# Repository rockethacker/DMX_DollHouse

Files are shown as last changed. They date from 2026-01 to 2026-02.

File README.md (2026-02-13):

# DMX_DollHouse
DMX Controller for Haunted Doll House

# Development Environment Setup
1. Install Github Desktop from https://desktop.github.com/download/
2. Open Github Desktop and sign in. Create account if needed.
3. In Github Desktop clone this repo
   1. "File --> Clone repository..."
   2. Select "URL" tab
   3. Enter "rockethacker/DMX_DollHouse" into URL field
   4. Note that this will clone to your documents folder
5. Install Arduino IDE from https://www.arduino.cc/en/software/#ide
6. Open Arduino IDE
7. Install board definition
   1. Open "Tools --> Board --> Boards Manager..."
   2. search for "esp"
   3. Install "esp32 by Espressif Systems" version 3.1.0
   4. If it times out, try this https://forum.arduino.cc/t/downloading-esp32-3-3-5-fails/1420739/7
8. Note that the above installations should take care of the CH340 driver installation. If not, follow https://learn.sparkfun.com/tutorials/how-to-install-ch340-drivers
9. Install Libraries
   1. Open "Tools --> Manage Libraries..."
   1. Install "esp_dmx by Mitch Weisbrod" version 4.1.0
      1. dmx read example won't compile, https://github.com/someweisguy/esp_dmx/issues/181#issuecomment-2619261884
      1. update uart.c to fork version
   1. Install "Freenove WS2812 Lib for ESP32" version 2.0.1
   2. Install "SparkFun Qwiic Relay Arduino Library" version 1.3.1
   3. Install "Adafruit SH110X" v2.1.14 with dependencies
10. Plug in Sparkfun Thing Plus via USB C cable
11. Select board by selecting "Tools --> Board --> esp32 --> SparkFun ESP32 Thing Plus C" 
12. Select port by selecting "Tools -->  Port --> COMxx" Where "xx" is the port your board is connected to (e.g. COM3)
13. Open this project by selecting "File --> Open..." and navigating to "Documents\GitHub\DMX_DollHouse\DMX_DollHouse.ino"

# Hardware
Parts are mostly from SparkFun. If you're in the DFW area and buy from Mouser you can get very fast, cheap delivery (sometimes overnight) via USPS
* https://www.sparkfun.com/sparkfun-esp32-thing-plus-dmx-to-led-shield.html
* https://www.sparkfun.com/sparkfun-thing-plus-esp32-wroom-usb-c.html
* https://www.sparkfun.com/feather-stackable-header-set.html
  * headers for thing plus
* https://www.adafruit.com/product/6313 - FeatherWing 128x64 OLED with pins
* https://www.sparkfun.com/sparkfun-qwiic-quad-relay.html
  * Discontinued product but available on Mouser
* This code supports WS2812 LEDs
* Power connection is a 5.5mm barrel jack with positive center pin.

# Pin & Channel Designations
* Pinouts for SparkFun Thing (SFT) Plus C. J1 is the 16 pin header. J7 is the 12 pin header.
* For some reason, the DMX board documentation had the D1/D1 pins swapped

| SFT Pin | SFT GPIO | SFT Name | Connected To  |
| --- | --- | --- | --- |
| J1-13 | 19 | POCI | DMX D0 |
| J1-12 | 23 | PICO | DMX D1 |
| J7-6 | 27 | 11 | DMX D2 |
| J1-2 | 17 | TX | DMX Transmit  |
| J1-3 | 16 | RX | DMX Receive |
| J1-1 | 4 | FREE | DMX Enable |
| J7-5 | 15 | 08 | OLED Button A |
| J7-3 | 14 | 04 | OLED Button B |
| J7-4 | 32 | 06 | OLED Button C |

# DMX Universe Channels
* All Channels are Offset by the the starting address (default is 0 offset)
* Lighting values are 0-255
* Relay commands are boolean >127 is TRUE

| Chan | Function |
| ---- | --- |
| 1 | LED0 Red |
| 2 | LED0 Green  |
| 3 | LED0 Blue |
| 4 | LED0 Dimmer |
| 5 | LED1 Red |
| 6 | LED1 Green  |
| 7 | LED1 Blue |
| 8 | LED1 Dimmer |
| 9 | LED2 Red |
| 10 | LED2 Green  |
| 11 | LED2 Blue |
| 12 | LED2 Dimmer |
| 13 | Relay 1 |
| 14 | Relay 2 |
| 15 | Relay 3 |
| 16 | Relay 4 |

# Troubleshooting Notes
* "SparkFun DMX Shield Library" makes some bad assumptions on how to detect the beginning of the DMX frames so isn't reliabloe for DMX reading

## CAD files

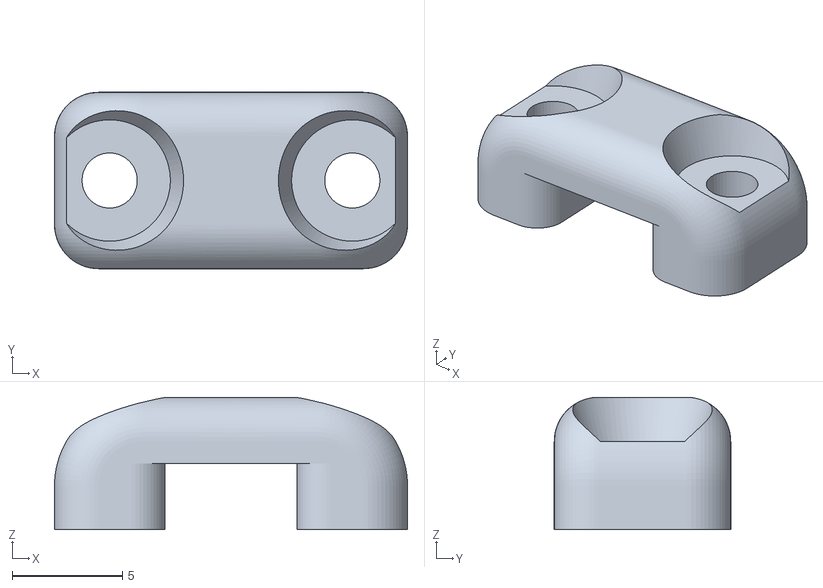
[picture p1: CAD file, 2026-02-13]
Enclosure/Clamp_LED.stl
16.0 x 8.00 x 6.00

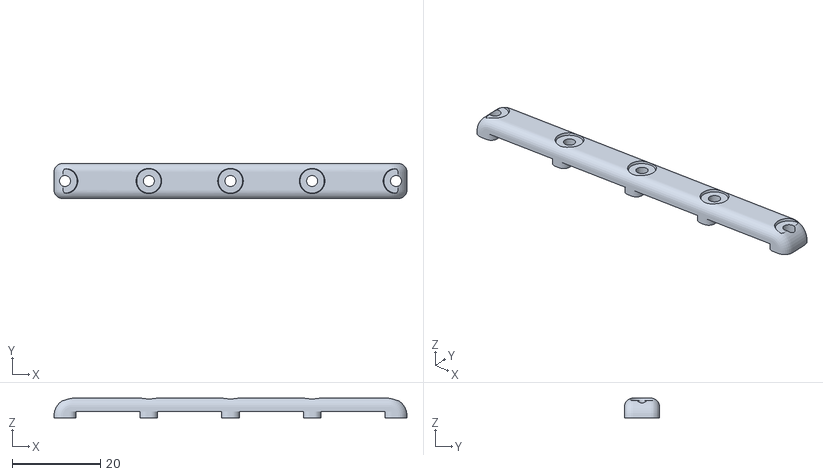
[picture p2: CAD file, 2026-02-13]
Enclosure/Clamp_Relay.stl
80.0 x 8.00 x 4.50

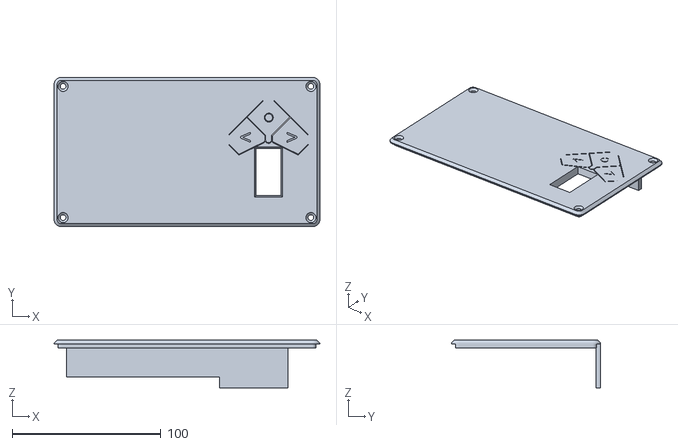
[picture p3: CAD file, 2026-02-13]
Enclosure/Box_Lid.stl
178.9 x 100.4 x 32.2

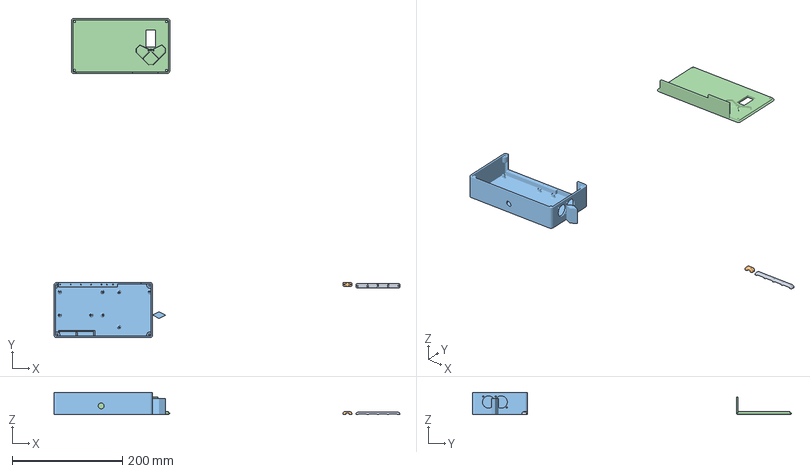
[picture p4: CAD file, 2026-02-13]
Enclosure/DollHouse.3mf
627.5 x 579.4 x 40.2 mm
Clamp_Relay.stl
Clamp_LED.stl
Box_Bottom.stl
Box_Lid.stl

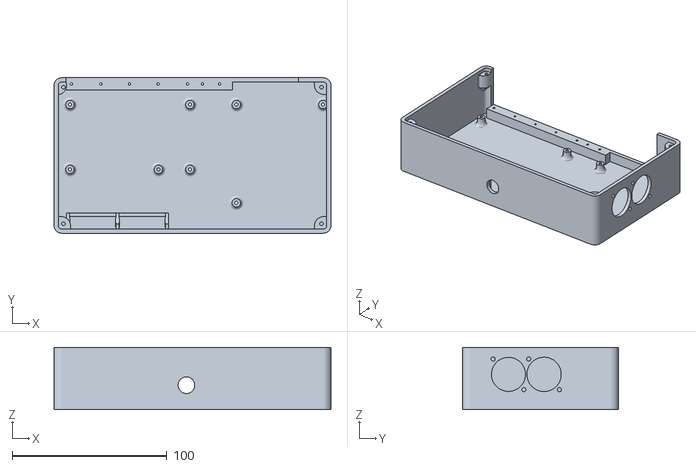
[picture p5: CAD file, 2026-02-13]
Enclosure/Box_Bottom.stl
178.9 x 100.4 x 40.2

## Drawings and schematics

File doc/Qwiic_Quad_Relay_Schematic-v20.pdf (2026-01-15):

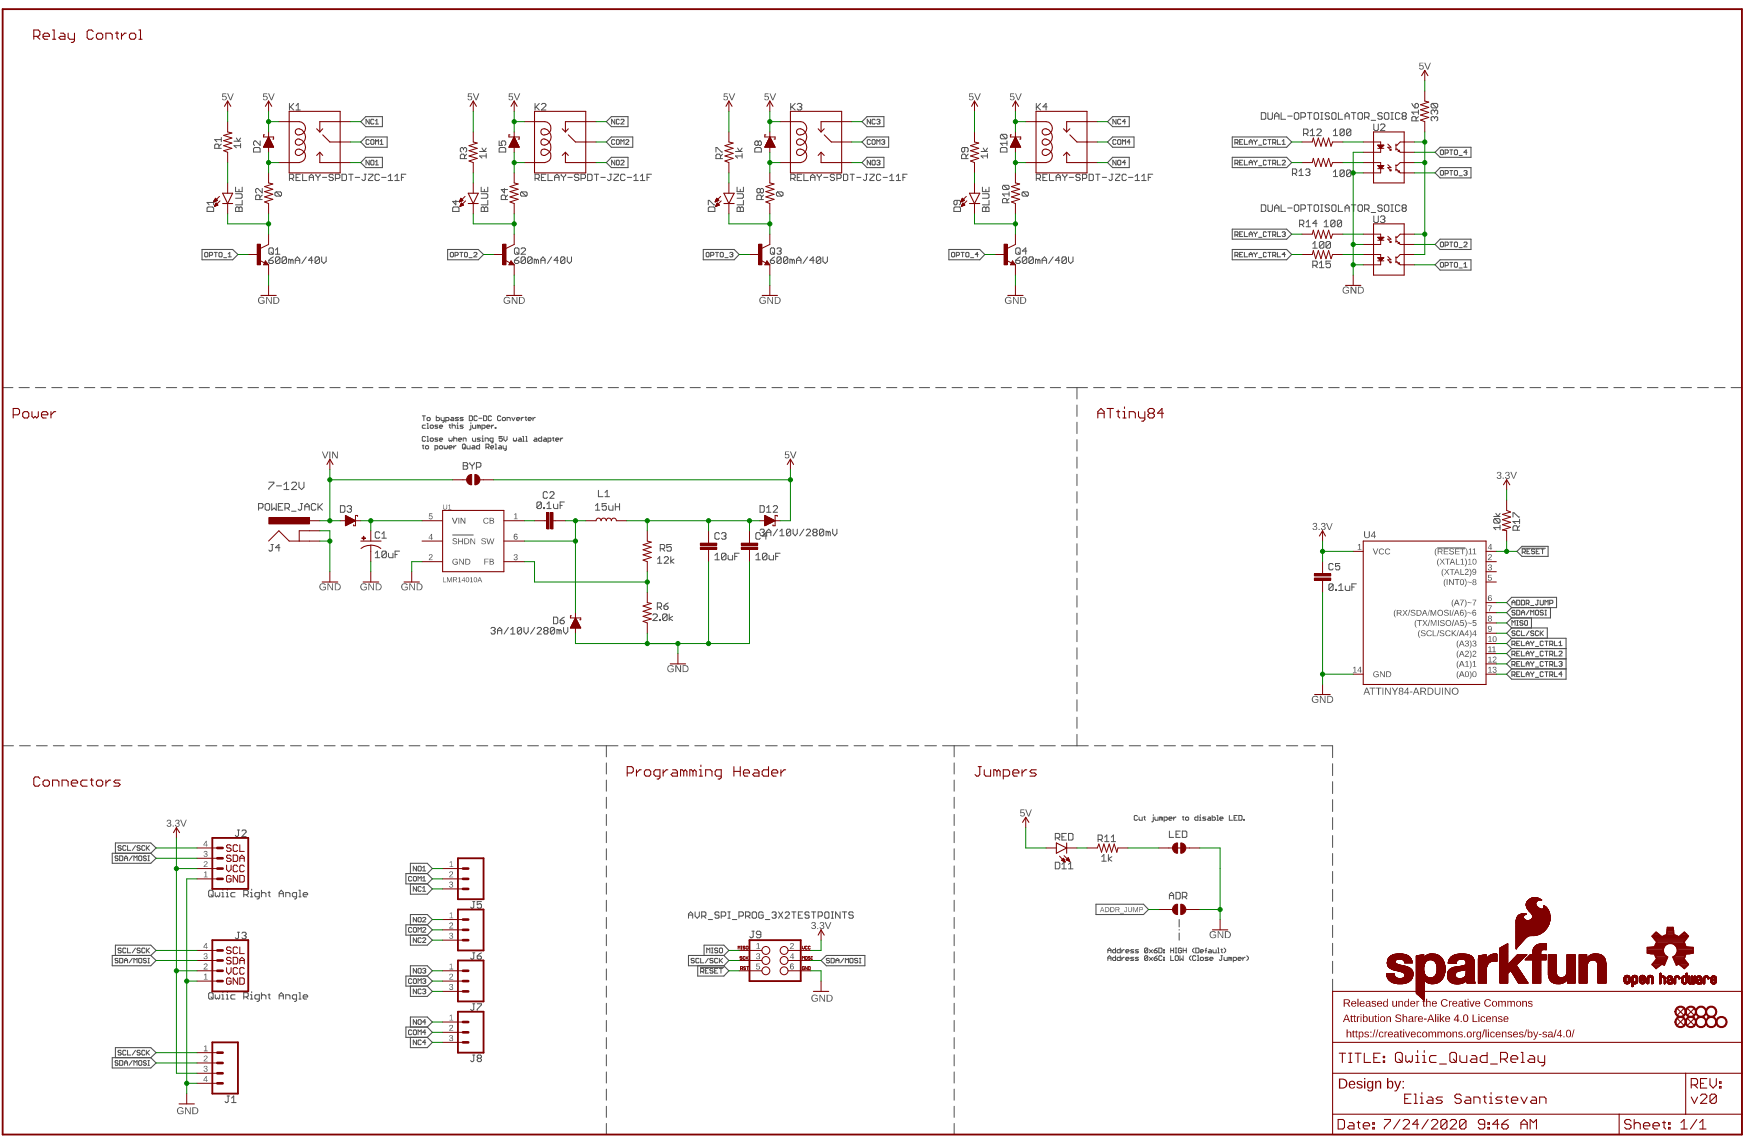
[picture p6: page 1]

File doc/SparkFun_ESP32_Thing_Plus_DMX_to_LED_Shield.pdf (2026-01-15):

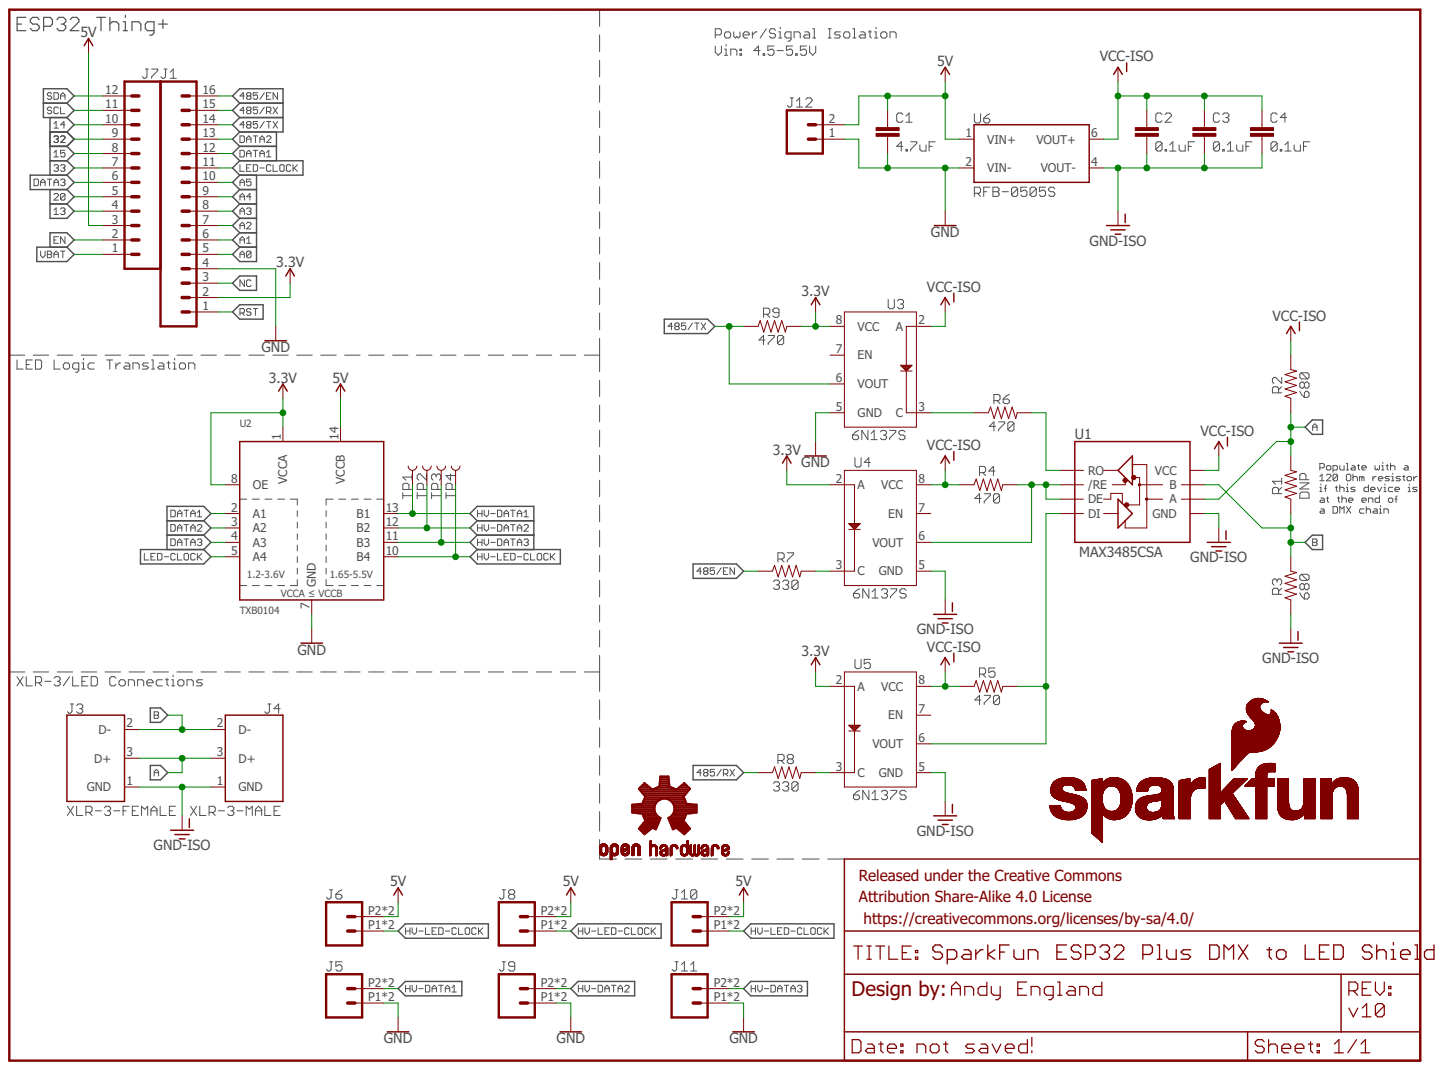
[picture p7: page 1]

Released under the Creative Commons Attribution Share-Alike 4.0 License https://creativecommons.org/licenses/by-sa/4.0/

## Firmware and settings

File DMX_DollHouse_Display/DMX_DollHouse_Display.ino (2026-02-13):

/*

  DMX Read

  This sketch allows you to read DMX from a DMX controller using a standard DMX
  shield, such SparkFun ESP32 Thing Plus DMX to LED Shield. This sketch was
  made for the Arduino framework!

  Created 9 September 2021
  By Mitch Weisbrod

  https://github.com/someweisguy/esp_dmx

*/
// DMX board libs
#include <Arduino.h>
#include <esp_dmx.h>
#include "Freenove_WS2812_Lib_for_ESP32.h"

//Relay Board Libs
#include <Wire.h>
#include "SparkFun_Qwiic_Relay.h"

//Display Libs
#include <SPI.h>
#include <Wire.h>
#include <Adafruit_GFX.h>
#include <Adafruit_SH110X.h>

// ==== DMX Init ==== //
// Define DMX bus
// Pins will differ between ESP32 models
int transmitPin = 17;
int receivePin = 16;
int enablePin = 4;

// Define port connected to DMX. ESP32 has either 2 or 3 ports.
// Port 0 is typically used to transmit serial data back to your Serial Monitor
dmx_port_t dmxPort = 1;

/* Now we want somewhere to store our DMX data. Since a single packet of DMX
  data can be up to 513 bytes long, we want our array to be at least that long.
  This library knows that the max DMX packet size is 513, so we can fill in the
  array size with `DMX_PACKET_SIZE`. */
byte data[DMX_PACKET_SIZE];

bool dmxIsConnected = false; //Connection status
unsigned long lastUpdate = millis(); //timer

// ==== LED Init ==== //
#define LEDS_COUNT  100 //Same LED count for all strips
// For some reason the documentation has pins 19 and 23 mixed up
#define LED0_PIN	19 //DMX board terminal D0. J1-pin 13 on Sparkfun Thing 
#define LED1_PIN	23 //DMX board terminal D1. J1-pin 12 on Sparkfun Thing
#define LED2_PIN	27 //DMX board terminal D2. J7-pin 6 on Sparkfun Thing

Freenove_ESP32_WS2812 LED0 = Freenove_ESP32_WS2812(LEDS_COUNT, LED0_PIN, 0, TYPE_GRB);
Freenove_ESP32_WS2812 LED1 = Freenove_ESP32_WS2812(LEDS_COUNT, LED1_PIN, 1, TYPE_GRB);
Freenove_ESP32_WS2812 LED2 = Freenove_ESP32_WS2812(LEDS_COUNT, LED2_PIN, 2, TYPE_GRB);

// ==== Relay Init ==== //
#define RELAY_ADDR 0x6D // Alternate address 0x6C

Qwiic_Relay quadRelay(RELAY_ADDR); 

// ==== Display Init ==== //
Adafruit_SH1107 display = Adafruit_SH1107(64, 128, &Wire);
uint16_t page_chan=0;
uint16_t page=0;
uint8_t data_val=0;

// ==== Program Init ==== //
//State machine states
enum states {
  DMX_SETUP, DMX_RUN, DMX
};

//Starting address in this DMX universe
//This device takes 16 channels
//baby board test is dmx start 1, ion perform is dmx 496
uint16_t dmxStartAddr = 496; 
int rate = 20; //rate in Hz

// a place to store packet information (not data)
dmx_packet_t packet;

void setup() {
  Serial.begin(115200); //Start serial monitor
  Serial.println("Initializing...");

// ==== DMX Init ==== //
  /* Install the DMX driver. Tell it which DMX port to use,
    what device configuration to use, and what DMX personalities it should have.
    If you aren't sure which configuration to use, you can use the macros
    `DMX_CONFIG_DEFAULT` to set the configuration to its default settings.
    This device is being setup as a DMX responder so it is likely that it should
    respond to DMX commands. It will need at least one DMX personality. Since
    this is an example, we will use a default personality which only uses 1 DMX
    slot in its footprint. */
  dmx_config_t config = DMX_CONFIG_DEFAULT;
  dmx_personality_t personalities[] = {
    {1, "Default Personality"}
  };
  int personality_count = 1;
  Serial.println("Installing dmx driver...");
  dmx_driver_install(dmxPort, &config, personalities, personality_count);
  Serial.println("dmx driver installed...");
  dmx_set_pin(dmxPort, transmitPin, receivePin, enablePin);

// ==== LED Init ==== //
  LED0.begin();
  LED0.setBrightness(0);
  LED1.begin();
  LED1.setBrightness(0);
  LED2.begin();
  LED2.setBrightness(0);

// ==== Relay Init ==== //
  Wire.begin(); 
  // Make sure the hardware is set up correctly.
  if(!quadRelay.begin())
    Serial.println("Check connections to Qwiic Relay.");
  else
    Serial.println("Ready to flip some switches.");
  
  // Make sure all relays are off
  quadRelay.turnAllRelaysOff(); 

// ==== Display Init ==== //
  delay(250); // wait for the OLED to power up
  display.begin(0x3C, true); // Address 0x3C default
  Serial.println("OLED begun");
  display.clearDisplay();
  display.setRotation(1);
  display.setTextSize(1);
  display.setTextColor(SH110X_WHITE);
}

void loop() {

  /* And now we wait! The DMX standard defines the amount of time until DMX
    officially times out. That amount of time is converted into ESP32 clock
    ticks using the constant `DMX_TIMEOUT_TICK`. If it takes longer than that
    amount of time to receive data, this if statement will evaluate to false. */
  if (dmx_receive(dmxPort, &packet, DMX_TIMEOUT_TICK)) {
    
    //we've received DMX data!
    unsigned long now = millis(); //Record when we received new data

    // If no DMX errors, do things
    if (!packet.err) {

      //On first packet, log successful connection
      if (!dmxIsConnected) {
        Serial.println("DMX is connected!");
        Serial.println(packet.size-1, DEC); //list DMX packet size
        dmxIsConnected = true;
      }
      
      // Print results to serial at rate
      if (now - lastUpdate > 1000/rate) {
        
        dmx_read(dmxPort, data, packet.size); //copy data into buffer
        
        /* Print the received start code - it's usually 0. */
        //Serial.printf("Start code is 0x%02X and slot 1 is 0x%02X\n", data[0], data[1]);
        
        // Data has been received, print out channel values to serial
        Serial.print(dmxStartAddr, DEC);
        Serial.print(" : ");
        for (uint16_t i = 0; i < 16; i++) {
          data_val = data[dmxStartAddr+i];
          if (data_val > 0xF){
            Serial.print(data_val, HEX);
          } else {
            Serial.print(" "); //pad single digit with space
            Serial.print(data_val, HEX);
          }
          Serial.print(" "); //space between entries
        }
       /*
        // write all channel values to serial
        for (uint16_t i = 1; i <=512; i++) {
            Serial.print(data[i], HEX);
            Serial.print(" ");
        }
        */
        
        Serial.println(" ");
        
        //Output color commands to LED strips
        LED0.setAllLedsColorData(data[dmxStartAddr+0], data[dmxStartAddr+1], data[dmxStartAddr+2]);
        LED0.setBrightness(data[dmxStartAddr+3]);
        LED0.show();
        LED1.setAllLedsColorData(data[dmxStartAddr+4], data[dmxStartAddr+5], data[dmxStartAddr+6]);
        LED1.setBrightness(data[dmxStartAddr+7]);
        LED1.show();
        LED2.setAllLedsColorData(data[dmxStartAddr+8], data[dmxStartAddr+9], data[dmxStartAddr+10]);
        LED2.setBrightness(data[dmxStartAddr+11]);
        LED2.show();

        //Output commands to relays
        if(data[dmxStartAddr+12]>127)
          quadRelay.turnRelayOn(1); 
        else
          quadRelay.turnRelayOff(1);

        if(data[dmxStartAddr+13]>127)
          quadRelay.turnRelayOn(2); 
        else
          quadRelay.turnRelayOff(2);

        if(data[dmxStartAddr+14]>127)
          quadRelay.turnRelayOn(3); 
        else
          quadRelay.turnRelayOff(3);

        if(data[dmxStartAddr+15]>127)
          quadRelay.turnRelayOn(4); 
        else
          quadRelay.turnRelayOff(4);

        // ==== Output to Display ==== //
       
        // Data has been received, print out channel values to display
        display.clearDisplay();
        display.setCursor(0,0);
        display.print("START: ");
        display.println(dmxStartAddr, DEC);
        for (uint16_t i = 0; i < 16; i++) {
          data_val = data[dmxStartAddr+i];
          if (data_val > 0xF){
            display.print(data_val, HEX);
          } else {
            display.print(" "); //pad single digit with space
            display.print(data_val, HEX);
          }
          display.print(" "); //space between entries
          if (i%4>=3) {display.println(" ");}
        }
        display.display(); // actually display all of the above

       /*
        //For each page. 8 channels per line. 8 lines per page.
        //for (page=0; page<=7; page++){
          display.clearDisplay();
          display.setCursor(105,0);
          display.print(page%8*64, DEC);
          display.setCursor(0,0);
          for (page_chan=0; page_chan <= 63; page_chan++){
            data_val = data[page%8*64+1];
            //If single digit, pad with space
            if (data_val > 0xF){
              display.print(data_val, HEX);
            } else {
              display.print(" ");
              display.print(data_val, HEX);
            }
            
            if (page_chan%8>=7) {display.println(" ");}
          }
          display.display(); // actually display all of the above
          page++;
          */
        //}
        lastUpdate = now;
      }
    } else {
      /* Oops! A DMX error occurred! Don't worry, this can happen when you first
        connect or disconnect your DMX devices. If you are consistently getting
        DMX errors, then something may have gone wrong with your code or
        something is seriously wrong with your DMX transmitter. */
      Serial.println("A DMX error occurred.");
    }
  } else if (dmxIsConnected) {
    /* If DMX times out after having been connected, it likely means that the
      DMX cable was unplugged. When that happens in this example sketch, we'll
      uninstall the DMX driver. */
    Serial.println("DMX was disconnected.");
    //dmx_driver_delete(dmxPort);

  }
}

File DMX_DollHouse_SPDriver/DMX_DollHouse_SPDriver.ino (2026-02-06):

/* https://github.com/rockethacker/DMX_DollHouse

== Description ==
- Inputs DMX commands and applies to LED, servo and Relay outputs
- Pinouts below are for SparkFun Thing Plus C. Variants of SparkFun Things will have different pin designations, see their graphical datasheet.
- See README for hardware requirements

== Resources ==
https://learn.sparkfun.com/tutorials/installing-an-arduino-library
https://learn.adafruit.com/assets/139874
https://www.youtube.com/shorts/y7VVxOw890M - How to properly press boot button to upload code

== Libraries ==
- SparkFun DMX Shield Library https://github.com/sparkfun/SparkFunDMX

*/

// Inlcude DMX library
//#include "libraries\SparkFun_DMX_Shield_Library\SparkFunDMX.h"
#include "SparkFunDMX.h"

// Create DMX object
SparkFunDMX dmx;

// Create serial port to be used for DMX interface. Exact implementation depends
// on platform, this example is for the ESP32
HardwareSerial dmxSerial(1);  //originally was set to 2, but this board uses port 1, pins 16/17

// Enable pin for DMX shield (Free pin on Thing Plus or Feather pinout)
uint8_t enPin = 4;

// Number of DMX channels, can be up to 512
uint16_t numChannels = 192;

// Buffer to store DMX data
#define buffer_size 16
uint8_t buffer[buffer_size];


void setup()
{
    Serial.begin(115200);
    Serial.println("SparkFun DMX Example 2 - Input");

    // Begin DMX serial port
    // RX and TX pins explicitly defined for ESP32 Thing Plus
    //dmxSerial.begin(DMX_BAUD, DMX_FORMAT,16,17);
    dmxSerial.begin(DMX_BAUD, DMX_FORMAT);

    // Begin DMX driver
    dmx.begin(dmxSerial, enPin, numChannels);

    // Set communicaiton direction, which can be changed on the fly as needed
    dmx.setComDir(DMX_READ_DIR);

    Serial.println("DMX initialized!");
}

void loop()
{
    // Wait until data has been received
    while(dmx.dataAvailable() == false)
    {
        // Must called update() to actually check for received data
        dmx.update();
    }

    // Data has been received, read out channels
    dmx.readBytes(buffer, buffer_size);
    for (uint8_t i = 0; i < buffer_size; i++) {
        Serial.print(buffer[i], HEX);
        Serial.print(" ");
    }
    Serial.println(" ");
    

}

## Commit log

2026-02-06 added led support
2026-02-09 added two more LED channels
    [Box_Bottom.stl, Clamp_LED.stl, Clamp_Relay.stl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]
2026-02-09 fixed D0/1 pin swap
    [DMX_DollHouse.ino]
2026-02-09 added relay board
    [Box_Lid.stl, DollHouse.3mf]
2026-02-09 latest bottom
    [Box_Bottom.stl, DollHouse.3mf]
2026-02-13 added display
    [Box_Bottom.stl, Box_Lid.stl, Clamp_LED.stl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]
2026-02-13 Update DMX_DollHouse_Display.ino
    fixed data type bug
    improved serial display
    [DMX_DollHouse_Display.ino]
